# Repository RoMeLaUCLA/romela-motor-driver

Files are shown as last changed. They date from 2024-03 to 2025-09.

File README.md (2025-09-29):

# RoMeLa motor driver gen2
 Motor driver PCB and firmware designed for RoMeLa actuators. 
 
 Block diagram of the hardware:
 
 

 ## System Diagram

 
 
 # PCB reference

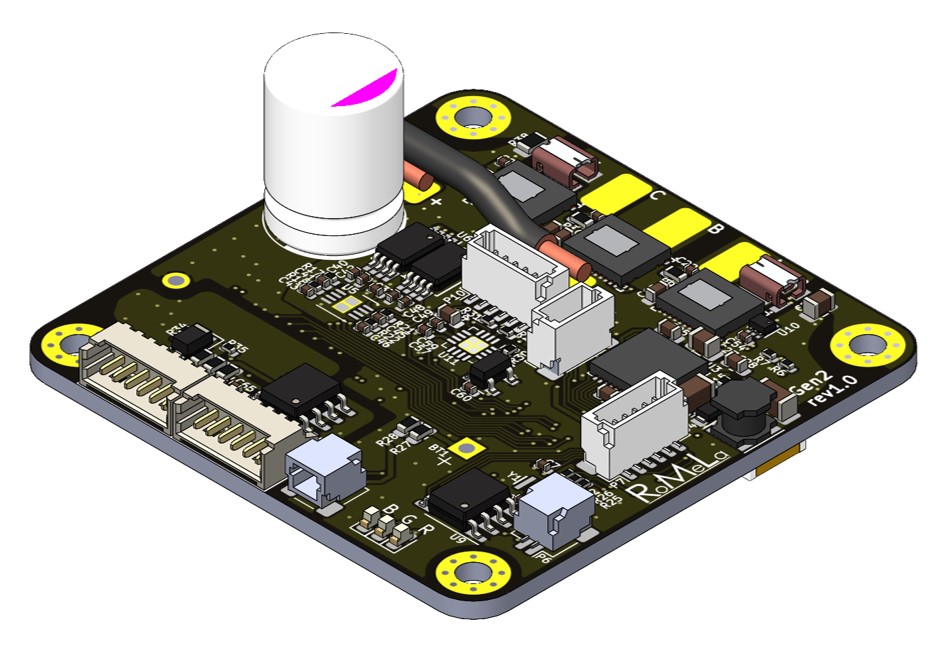
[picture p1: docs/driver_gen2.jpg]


[Link to gen2 schematics](/pcb/rev1/schematics_Motor_Gen2.pdf)

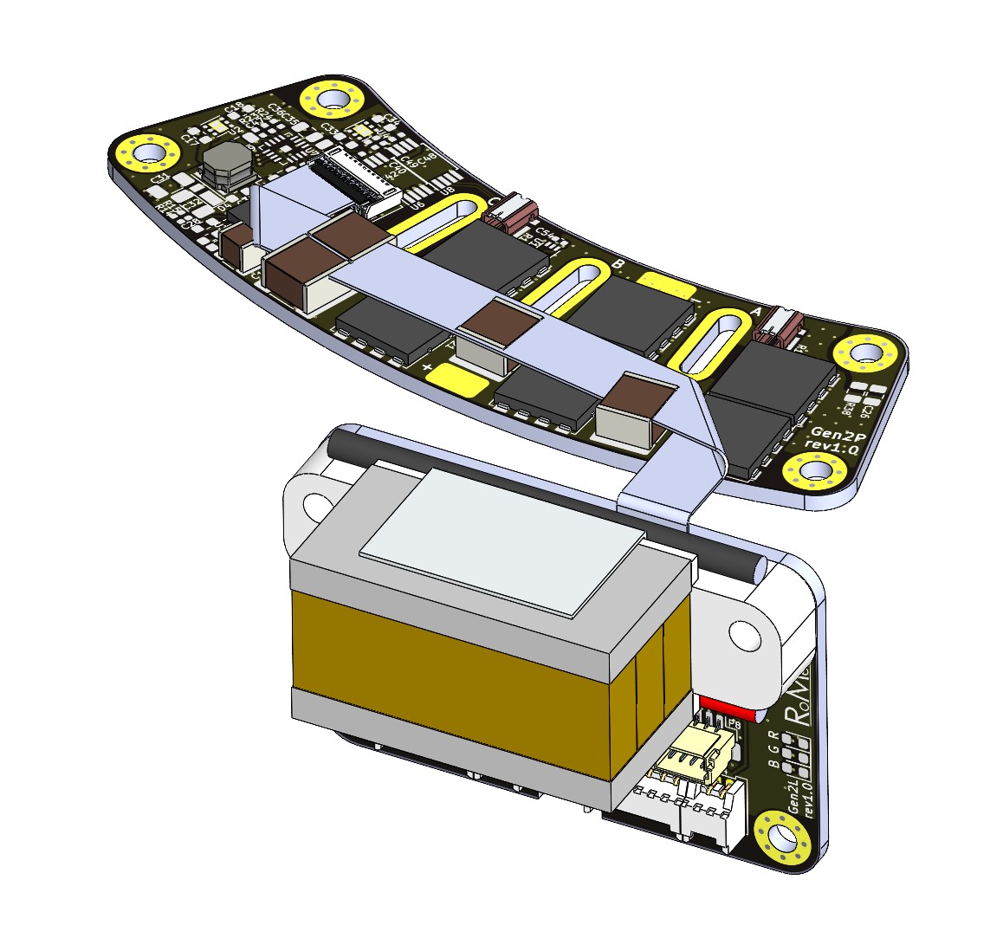
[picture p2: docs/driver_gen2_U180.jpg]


[Link to gen2L schematics](/pcb/split/gen2L/schematics_Motor_Gen2L.pdf)

[Link to gen2P schematics](/pcb/split/gen2P/schematics_Motor_Gen2P.pdf)

# Change Log
12/1/2022 Ver. 581
- First version using gcc(STM32CubeIDE)

04/13/2022 Ver. 48D
- Added 0.5ms de-glitch time for E-Stop input and 1sec minimum E-Stop time.

02/09/2022 Ver. 449
- Fixed MCU lock up with RS-485 over run present in Ver. 2BB.

09/27/2021 Ver. 33B
- Random ABS Posi error and Init error on power-up.

05/27/2021 Ver. 2BB
- Fixed cogging torque comp. issue.

03/31/2021 Ver. 27F
- Limit Id Max changed to Limit Acc Max
- Limit Iq Max changed to Limit I Max
- Added external Estop signal (wiring change) and command
- Acceleration limited S curve added to Mode 2 (position mode).
- Goal velocity and Iq feedforward term enabled for Mode 3. (Allow Id, Iq, Velocity, Position reference all at once)

09/29/2020 Ver. 130-137
- Added support for KB01_R18 and KB01_R24. (External AS5047 Encoder)

06/23/2020 Ver. D7
- Fixed joint limit issue.

05/20/2020 Ver. B4
- GEN2 Initial release.

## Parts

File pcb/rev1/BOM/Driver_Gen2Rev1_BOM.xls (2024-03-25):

Manufacturer | Manufacturer Part Number | Designator | Qty | Description | Case | SMD ,BGA,LLC(QFN),ORTH | Top/Bottom | points | Total points | polarity | Notes | Comments
Samsung Electro-Mechanics | CL05B104KO5NFNC | C1-C5, C7, C16, C37, C40, C48, C50, C54, C55, C57, C59, C60, C62, C63, C65 | 19 | 0.1µF ±10% 16V Ceramic Capacitor X7R 0402 | 0402 | SMD | Top and Bottom | 2 | 38 |  | Alternative parts accepted upon approval
 |  | C8 | 1 | D.N.P.
TDK Corporation | C5750X7S2A106K230KE | C9-C15 | 7 | 10µF ±10% 100V Ceramic Capacitor X7S 2220 | 2220 | SMD | Bottom | 2 | 14 |  | Alternative parts accepted upon approval
Samsung Electro-Mechanics | CL10B103KC8WPNC | C19-C21 | 3 | 10000pF ±10% 100V Ceramic Capacitor X7R 0603 | 0603 | SMD | Top | 2 | 6 |  | Alternative parts accepted upon approval
Murata Electronics | GCM155R72A472KA37D | C22-C24 | 3 | 4700pF ±10% 100V Ceramic Capacitor X7R 0402 | 0402 | SMD | Top | 2 | 6 |  | Alternative parts accepted upon approval
Samsung Electro-Mechanics | CL10B104KC8NNNC | C25 | 1 | 0.1µF ±10% 100V Ceramic Capacitor X7R 0603 | 0603 | SMD | Top | 2 | 2 |  | Alternative parts accepted upon approval
KEMET | C0805W472KDRACTU | C26 | 1 | 4700pF ±10% 1000V (1kV) Ceramic Capacitor X7R 0805 | 0805 | SMD | Top | 2 | 2 |  | Alternative parts accepted upon approval
Samsung Electro-Mechanics | CL21B105KOFNNNG | C27 | 1 | 1µF ±10% 16V Ceramic Capacitor X7R 0805 | 0805 | SMD | Top | 2 | 2 |  | Alternative parts accepted upon approval
TDK Corporation | C1608X7S2A473K080AB | C28 | 1 | 0.047µF ±10% 100V Ceramic Capacitor X7S 0603 | 0603 | SMD | Top | 2 | 2 |  | Alternative parts accepted upon approval
Samsung Electro-Mechanics | CL10B105KP8NFNC | C17, C18, C29, C33, C34, C58 | 6 | 1µF ±10% 10V Ceramic Capacitor X7R 0603 | 0603 | SMD | Top and Bottom | 2 | 12 |  | Alternative parts accepted upon approval
Samsung Electro-Mechanics | CL10B334KO8NFNC | C30 | 1 | 0.33µF ±10% 16V Ceramic Capacitor X7R 0603 | 0603 | SMD | Bottom | 2 | 2 |  | Alternative parts accepted upon approval
Samsung Electro-Mechanics | CL31B226KPHNNNE | C31, C61, C64 | 3 | 22µF ±10% 10V Ceramic Capacitor X7R 1206 | 1206 | SMD | Top and Bottom | 2 | 6 |  | Alternative parts accepted upon approval
TDK Corporation | CGA5L3X7S2A225K160AB | C32 | 1 | 2.2µF ±10% 100V Ceramic Capacitor X7S 1206 | 1206 | SMD | Top | 2 | 2 |  | Alternative parts accepted upon approval
Samsung Electro-Mechanics | CL21B106KPQNFNE | C6, C35, C36, C38, C39, C56 | 6 | 10µF ±10% 10V Ceramic Capacitor X7R 0805 | 0805 | SMD | Bottom | 2 | 12 |  | Alternative parts accepted upon approval
Samsung Electro-Mechanics | CL05B103KB5NNNC | C42, C49, C51-C53 | 5 | 10000pF ±10% 50V Ceramic Capacitor X7R 0402 | 0402 | SMD | Top and Bottom | 2 | 10 |  | Alternative parts accepted upon approval
Murata Electronics | GRM1555C1H102JA01J | C43, C46 | 2 | 1000pF ±5% 50V Ceramic Capacitor C0G, NP0 0402 | 0402 | SMD | Top | 2 | 4 |  | Alternative parts accepted upon approval
KEMET | C0402C152J5GAC7867 | C41, C44, C45, C47 | 4 | 1500pF ±5% 50V Ceramic Capacitor C0G, NP0 0402 | 0402 | SMD | Top and Bottom | 2 | 8 |  | Alternative parts accepted upon approval
Rohm Semiconductor | SML-D12U1WT86 | D1 | 1 | Red 620nm LED Indication - Discrete 2.2V 0603 | 0603 | SMD | Top | 2 | 2 | Yes | Alternative parts accepted upon approval
Rohm Semiconductor | SML-D13M8WT86 | D2 | 1 | Green 572nm LED Indication - Discrete 2.2V 0603 | 0603 | SMD | Top | 2 | 2 | Yes | Alternative parts accepted upon approval
Rohm Semiconductor | SMLD12BN1WT86 | D3 | 1 | Blue 470nm LED Indication - Discrete 2.9V 0603 | 0603 | SMD | Top | 2 | 2 | Yes | Alternative parts accepted upon approval
Vishay Semiconductor Diodes Division | V1PM10-M3/H | D4 | 1 | Diode Schottky 100V 1A | DO-219AD | SMD | Top | 2 | 2 | Yes
STMicroelectronics | ESDCAN02-2BWY | D5 | 1 | 44V Clamp 3A (8/20µs) Ipp Tvs Diode Surface Mount SOT-323-3 | SOT-323 | SMD | Bottom | 3 | 3
Littelfuse Inc. | SMF3.3 | D6 | 1 | 6.8V Clamp 30A Ipp Tvs Diode | SOD-123F | SMD | Top | 2 | 2 | Yes
Bel Fuse Inc. | 0ZCM0002FF2G | F1 | 1 | PTC Resettable Fuse 60V 20mA 0603 | 0603 | SMD | Top | 2 | 2
Murata Electronics | BLM15PX601SN1D | FB1, FB2 | 2 | 600 Ohms Ferrite Bead 0402 230mOhm | 0402 | SMD | Bottom | 2 | 4 |  | Alternative parts accepted upon approval
 |  | J1, J2 | 2 | D.N.P.
Laird-Signal Integrity Products | TYS4030220M-10 | L1 | 1 | 22µH Shielded Wirewound Inductor 1A | 4mmx4mm | SMD | Top | 2 | 2
JST Sales America Inc. | SM02B-SRSS-TB(LF)(SN) | P5, P6 | 2 | Connector Header Surface Mount, Right Angle 2 position 1.00mm | Header 2pin | SMD | Top | 4 | 8
JST Sales America Inc. | BM06B-SRSS-TBT(LF)(SN) | P7, P10 | 2 | Connector Header Surface Mount 6 position 1.00mm | header 6pin | SMD | Top | 8 | 16
JST Sales America Inc. | BM04B-SRSS-TBT(LF)(SN) | P8 | 1 | Connector Header Surface Mount 4 position 1.00mm | Header 4pin | SMD | Top | 6 | 6
Molex | 0545500871 | P9 | 1 | 8 Position FFC Top 0.50mm Surface Mount, Right Angle | FFC header | SMD | Bottom | 10 | 10
Texas Instruments | CSD88599Q5DC | Q1-Q3 | 3 | Mosfet Array 2 N-Channel (Half Bridge) 60V 12W Surface Mount 22-VSON-CLIP (5x6) | 22-VSON-CLIP (5x6) | VSON | Top | 11 | 33 | Yes
Rohm Semiconductor | ESR03EZPJ121 | R1, R3, R4, R27, R28 | 5 | 120 Ohms ±5% 0.25W 0603 Pulse Withstanding | 0603 | SMD | Top and Bottom | 2 | 10
Bourns Inc. | CR0402-FX-1302GLF | R2, R15, R18, R22, R30, R31 | 6 | 13 kOhms ±1% 0.063W, 1/16W Chip Resistor 0402 | 0402 | SMD | Top | 2 | 12 |  | Alternative parts accepted upon approval
Bourns Inc. | CR0603-JW-470ELF | R5 | 1 | 47 Ohms ±5% 0.1W, 1/10W Chip Resistor 0603 | 0603 | SMD | Bottom | 2 | 2 |  | Alternative parts accepted upon approval
Bourns Inc. | CR0402-FX-7502GLF | R6, R14, R34 | 3 | 75 kOhms ±1% 0.063W, 1/16W Chip Resistor 0402 | 0402 | SMD | Top | 2 | 6 |  | Alternative parts accepted upon approval
Bourns Inc. | CR0402-FX-3901GLF | R7, R25, R26, R35 | 4 | 3.9 kOhms ±1% 0.063W, 1/16W Chip Resistor 0402 | 0402 | SMD | Top | 2 | 8 |  | Alternative parts accepted upon approval
Bourns Inc. | CR0402-J/-000GLF | R8, R16, R29 | 3 | 0 Ohms Jumper 0402 | 0402 | SMD | Top and Bottom | 2 | 6 |  | Alternative parts accepted upon approval
Bourns Inc. | CR0603AF/-2R20EAS | R9-R11 | 3 | 2.2 Ohms ±1% 0.1W, 1/10W Chip Resistor 0603 | 0603 | SMD | Top | 2 | 6 |  | Alternative parts accepted upon approval
Vishay Dale | WSK12161L000FEA | R12, R13 | 2 | 1 mOhms ±1% 3W Chip Resistor Wide 1612 (3831 Metric) | Wide 1612 (3831 Metric) | SMD | Top | 4 | 8
Bourns Inc. | CR0402-FX-7501GLF | R17, R21 | 2 | 7.5 kOhms ±1% 0.063W, 1/16W Chip Resistor 0402 | 0402 | SMD | Top | 2 | 4 |  | Alternative parts accepted upon approval
Bourns Inc. | CR0402-FX-10R0GLF | R19, R20, R23, R24 | 4 | 10 Ohms ±1% 0.063W, 1/16W Chip Resistor 0402 | 0402 | SMD | Bottom | 2 | 8 |  | Alternative parts accepted upon approval
Rohm Semiconductor | ESR03EZPF10R0 | R32, R33 | 2 | 10 Ohms ±1% 0.25W 0603 Pulse Withstanding | 0603 | SMD | Top | 2 | 4
Rohm Semiconductor | ESR10EZPJ105 | R38 | 1 | 1 MOhms ±5% 0.4W, 2/5W Chip Resistor 0805 | 0805 | SMD | Top | 2 | 2
STMicroelectronics | STM32F446RET6 | U1 | 1 | ARM® Cortex®-M4 STM32F4 Microcontroller IC 32-Bit 180MHz 512KB (512K x 8) FLASH 64-LQFP (10x10) | LQFP-64 10x10mm P0.5mm | SMD | Bottom | 64 | 64 | Yes
Texas Instruments | TLV76733DRVR | U2 | 1 | Linear Voltage Regulator IC 3.3V 1A 6-WSON (2x2) | WSON-6 | WSON | Bottom | 7 | 7 | Yes
Texas Instruments | DRV8320RSRHAR | U3 | 1 | Multiphase Motor Driver Power MOSFET SPI 40-VQFN (6x6) | PVQFN-40 | QFN | Top | 41 | 41 | Yes
Texas Instruments | LP5912-5.0DRVR | U4 | 1 | Linear Voltage Regulator IC 5V 500mA 6-WSON (2x2) | WSON-6 | WSON | Bottom | 7 | 7 | Yes
Texas Instruments | OPA2320AIDRGR | U5 | 1 | General Purpose Amplifier 2 Circuit Rail-to-Rail 8-SON (3x3) | S-PWSON-N8 | WSON | Top | 9 | 9 | Yes
Texas Instruments | ADS8353IRTER | U7 | 1 | 16 Bit Analog to Digital Converter 2 Input 2 SAR 16-WQFN (3x3) | WQFN-16 | QFN | Bottom | 17 | 17 | Yes
Texas Instruments | INA240A1PWR | U6, U8 | 2 | Current Sense Amplifier 1 Circuit 8-TSSOP | TSSOP-8 | SMD | Top | 8 | 16 | Yes
Maxim Integrated | MAX31855KASA+T | U9 | 1 | IC CONV THERMOCOUPLE-DGTL 8SOIC | SOIC-8 | SMD | Top | 8 | 8 | Yes
Texas Instruments | TMP112NAIDRLR | U10 | 1 | Temperature Sensor Digital, Local -40°C ~ 125°C 12 b SOT-563 | SOT-563 | SMD | Top | 6 | 6 | Yes
iC-Haus | iC-PV | U11 | 1 | - | QFN-16 | QFN | Top | 17 | 17 | Yes | Provided by customer
iC-Haus | iC-MHM | U12 | 1 | - | QFN-28 | QFN | Bottom | 29 | 29 | Yes | Provided by customer
Microchip Technology | 24LC16BT-E/OT | U13 | 1 | EEPROM Memory IC 16Kb (2K x 8) I²C 400kHz 900ns SOT-23-5 | SOT-23-5 | SMD | Top | 5 | 5
Texas Instruments | ISOW7842FDWE | U14 | 1 | General Purpose Digital Isolator 5000Vrms 4 Channel 100Mbps 100kV/µs CMTI 16-SOIC | SOIC-16W | SMD | Bottom | 16 | 16 | Yes
Maxim Integrated | MAX14775EASA+ | U15 | 1 | 1/1 Transceiver Half RS422, RS485 8-SOIC | 8-SOIC | SMD | Top | 8 | 8 | Yes
Murata Electronics | CSTNE8M00GH5C000R0 | Y1 | 1 | 8MHz Ceramic Resonator Built in Capacitor 33pF ±0.13% 40 Ohms -40°C ~ 125°C Surface Mount | 3.2mmx1.3mm | SMD | Top | 3 | 3

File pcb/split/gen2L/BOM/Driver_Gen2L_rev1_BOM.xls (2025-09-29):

Manufacturer | Manufacturer Part Number | Designator | Qty | Description | Case | SMD ,BGA,LLC(QFN),ORTH | Top/Bottom | points | Total points | polarity | Notes | Comments
Samsung Electro-Mechanics | CL21B106KPQNFNE | C6 | 1 | 10µF ±10% 10V Ceramic Capacitor X7R 0805 | 0805 | SMD | Bottom | 2 | 2 |  | Alternative parts accepted upon approval
Samsung Electro-Mechanics | CL05B104KA5NNNC | C1-C5, C7, C16, C50, C62, C63, C65 | 11 | 0.1 µF ±10% 25V Ceramic Capacitor X7R 0402 (1005 Metric) | 0402 | SMD | Top/Bottom | 2 | 22 |  | Alternative parts accepted upon approval
Samsung Electro-Mechanics | CL05B103KB5NNNC | C51-C53 | 3 | 10000pF ±10% 50V Ceramic Capacitor X7R 0402 | 0402 | SMD | Bottom | 2 | 6 |  | Alternative parts accepted upon approval
Samsung Electro-Mechanics | CL31B226KPHNNNE | C61, C64 | 2 | 22µF ±10% 10V Ceramic Capacitor X7R 1206 | 1206 | SMD | Bottom | 2 | 4 |  | Alternative parts accepted upon approval
Rohm Semiconductor | SML-D12U1WT86 | D1 | 1 | Red 620nm LED Indication - Discrete 2.2V 0603 | 0603 | SMD | Top | 2 | 2 | Yes | Alternative parts accepted upon approval
Rohm Semiconductor | SML-D13M8WT86 | D2 | 1 | Green 572nm LED Indication - Discrete 2.2V 0603 | 0603 | SMD | Top | 2 | 2 | Yes | Alternative parts accepted upon approval
Rohm Semiconductor | SMLD12BN1WT86 | D3 | 1 | Blue 470nm LED Indication - Discrete 2.9V 0603 | 0603 | SMD | Top | 2 | 2 | Yes | Alternative parts accepted upon approval
STMicroelectronics | ESDCAN02-2BWY | D5 | 1 | 44V Clamp 3A (8/20µs) Ipp Tvs Diode Surface Mount SOT-323-3 | SOT-323 | SMD | Top | 3 | 3
Littelfuse Inc. | SMF3.3 | D6 | 1 | 6.8V Clamp 30A Ipp Tvs Diode | SOD-123F | SMD | Bottom | 2 | 2 | Yes | Alternative: PTVS3V3S1UTR,115
Bel Fuse Inc. | 0ZCM0002FF2G | F1 | 1 | PTC Resettable Fuse 60V 20mA 0603 | 0603 | SMD | Bottom | 2 | 2
Murata Electronics | BLM15PX601SN1D | FB1, FB2 | 2 | 600 Ohms Ferrite Bead 0402 230mOhm | 0402 | SMD | Bottom | 2 | 4 |  | Alternative parts accepted upon approval
Molex | 5019122190 | J1 | 1 | 21 Position FPC Connector Contacts, Bottom 0.012" (0.30mm) Surface Mount, Right Angle | FPC 21POS | SMD | Top | 23 | 23
Molex | 5034800800 | J2, P9 | 2 | 8 Position FFC, FPC Connector Contacts, Top and Bottom 0.020" (0.50mm) Surface Mount, Right Angle | FPC 8POS | SMD | Top | 10 | 20
Molex | 0530480650 | P1, P2 | 2 | Connector Header Through Hole, Right Angle 6 position 0.049" (1.25mm) | Header R/A 6POS | TH | Top | 6 | 12
Molex | 0530480250 | P4, P5 | 2 | Connector Header Through Hole, Right Angle 2 position 0.049" (1.25mm) | Header R/A 2POS | TH | Top | 2 | 4
JST Sales America Inc. | SM02B-SRSS-TB(LF)(SN) | P6 | 1 | Connector Header Surface Mount, Right Angle 2 position 1.00mm | Header 2pin | SMD | Top | 4 | 4
JST Sales America Inc. | BM06B-SRSS-TB(LF)(SN) | P7, P10 | 2 | Connector Header Surface Mount 6 position 1.00mm | header 6pin | SMD | Top | 8 | 16
JST Sales America Inc. | BM04B-SRSS-TB(LF)(SN) | P8 | 1 | Connector Header Surface Mount 4 position 1.00mm | Header 4pin | SMD | Top | 6 | 6
Rohm Semiconductor | ESR03EZPJ121 | R1, R3, R4 | 3 | 120 Ohms ±5% 0.25W 0603 Pulse Withstanding | 0603 | SMD | Top/Bottom | 2 | 6 |  | Alternative parts accepted upon approval
Bourns Inc. | CR0402-FX-1302GLF | R2 | 1 | 13 kOhms ±1% 0.063W, 1/16W Chip Resistor 0402 | 0402 | SMD | Bottom | 2 | 2 |  | Alternative parts accepted upon approval
Bourns Inc. | CR0603-JW-470ELF | R5 | 1 | 47 Ohms ±5% 0.1W, 1/10W Chip Resistor 0603 | 0603 | SMD | Bottom | 2 | 2 |  | Alternative parts accepted upon approval
Bourns Inc. | CR0402-FX-3901GLF | R25, R26, R35 | 3 | 3.9 kOhms ±1% 0.063W, 1/16W Chip Resistor 0402 | 0402 | SMD | Top/Bottom | 2 | 6 |  | Alternative parts accepted upon approval
Rohm Semiconductor | ESR03EZPF10R0 | R32, R33 | 2 | 10 Ohms ±1% 0.25W 0603 Pulse Withstanding | 0603 | SMD | Top | 2 | 4 |  | Alternative parts accepted upon approval
Bourns Inc. | CR0402-FX-7502GLF | R34 | 1 | 75 kOhms ±1% 0.063W, 1/16W Chip Resistor 0402 | 0402 | SMD | Top | 2 | 2 |  | Alternative parts accepted upon approval
STMicroelectronics | STM32F446RET6 | U1 | 1 | ARM® Cortex®-M4 STM32F4 Microcontroller IC 32-Bit 180MHz 512KB (512K x 8) FLASH 64-LQFP (10x10) | LQFP-64 10x10mm P0.5mm | SMD | Bottom | 64 | 64 | Yes | Provided by customer
Maxim Integrated | MAX31855KASA+T | U9 | 1 | IC CONV THERMOCOUPLE-DGTL 8SOIC | SOIC-8 | SMD | Bottom | 8 | 8 | Yes | Provided by customer
Texas Instruments | ISOW7842FDWE | U14 | 1 | General Purpose Digital Isolator 5000Vrms 4 Channel 100Mbps 100kV/µs CMTI 16-SOIC | SOIC-16W | SMD | Bottom | 16 | 16 | Yes | Provided by customer
Maxim Integrated | MAX14775EASA+ | U15 | 1 | 1/1 Transceiver Half RS422, RS485 8-SOIC | 8-SOIC | SMD | Top | 8 | 8 | Yes | Provided by customer
Murata Electronics | CSTNE8M00GH5C000R0 | Y1 | 1 | 8MHz Ceramic Resonator Built in Capacitor 33pF ±0.13% 40 Ohms -40°C ~ 125°C Surface Mount | 3.2mmx1.3mm | SMD | Top | 3 | 3

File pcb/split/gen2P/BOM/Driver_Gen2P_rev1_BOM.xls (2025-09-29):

Manufacturer | Manufacturer Part Number | Designator | Qty | Description | Case | SMD ,BGA,LLC(QFN),ORTH | Top/Bottom | points | Total points | polarity | Notes | Comments
TDK Corporation | C5750X7S2A226M280KB | C9-C12 | 4 | 22 µF ±20% 100V Ceramic Capacitor X7S 2220 (5750 Metric) | 2220 | SMD | Top | 2 | 8 |  | Provided by customer
Murata Electronics | GRM32EC72A106KE05L | C15 | 1 | 10 µF ±10% 100V Ceramic Capacitor X7S 1210 (3225 Metric) | 1210 | SMD | Top | 2 | 2 |  | Alternative parts accepted upon approval
Samsung Electro-Mechanics | CL10B103KC8WPNC | C19-C21 | 3 | 10000pF ±10% 100V Ceramic Capacitor X7R 0603 | 0603 | SMD | Top | 2 | 6 |  | Alternative parts accepted upon approval
Samsung Electro-Mechanics | CL10B104KC8NNNC | C25 | 1 | 0.1µF ±10% 100V Ceramic Capacitor X7R 0603 | 0603 | SMD | Top | 2 | 2 |  | Alternative parts accepted upon approval
KEMET | C0805W472KDRACTU | C26 | 1 | 4700pF ±10% 1000V (1kV) Ceramic Capacitor X7R 0805 | 0805 | SMD | Top | 2 | 2 |  | Alternative parts accepted upon approval
Murata Electronics | GRM188Z71C225ME43J | C27 | 1 | 2.2 µF ±20% 16V Ceramic Capacitor X7R 0603 (1608 Metric) | 0603 | SMD | Top | 2 | 2 |  | Alternative parts accepted upon approval
Würth Elektronik | 885012206118 | C28 | 1 | 0.047 µF ±10% 100V Ceramic Capacitor X7R 0603 (1608 Metric) | 0603 | SMD | Top | 2 | 2 |  | Alternative parts accepted upon approval
Samsung Electro-Mechanics | CL10B105KP8NFNC | C17, C18, C29, C33, C34 | 5 | 1µF ±10% 10V Ceramic Capacitor X7R 0603 | 0603 | SMD | Top | 2 | 10 |  | Alternative parts accepted upon approval
Samsung Electro-Mechanics | CL10B334KO8NFNC | C30 | 1 | 0.33µF ±10% 16V Ceramic Capacitor X7R 0603 | 0603 | SMD | Top | 2 | 2 |  | Alternative parts accepted upon approval
Samsung Electro-Mechanics | CL31B226KPHNNNE | C31 | 1 | 22µF ±10% 10V Ceramic Capacitor X7R 1206 | 1206 | SMD | Top | 2 | 2 |  | Alternative parts accepted upon approval
Samsung Electro-Mechanics | CL31B225KCHSNNE | C32 | 1 | 2.2 µF ±10% 100V Ceramic Capacitor X7R 1206 (3216 Metric) | 1206 | SMD | Top | 2 | 2 |  | Alternative parts accepted upon approval
Samsung Electro-Mechanics | CL21B106KPQNFNE | C35, C36, C38, C39 | 4 | 10µF ±10% 10V Ceramic Capacitor X7R 0805 | 0805 | SMD | Top | 2 | 8 |  | Alternative parts accepted upon approval
Samsung Electro-Mechanics | CL05B104KA5NNNC | C40, C48, C54 | 3 | 0.1 µF ±10% 25V Ceramic Capacitor X7R 0402 (1005 Metric) | 0402 | SMD | Top | 2 | 6 |  | Alternative parts accepted upon approval
Samsung Electro-Mechanics | CL05B103KB5NNNC | C42, C49 | 2 | 10000pF ±10% 50V Ceramic Capacitor X7R 0402 | 0402 | SMD | Top | 2 | 4 |  | Alternative parts accepted upon approval
Murata Electronics | GRM1555C1H102JA01D | C44, C47 | 2 | 1000 pF ±5% 50V Ceramic Capacitor C0G, NP0 0402 (1005 Metric) | 0402 | SMD | Top | 2 | 4 |  | Alternative parts accepted upon approval
Vishay General Semiconductor - Diodes Division | V1PM10HM3/H | D4 | 1 | Diode Schottky 100 V 1A Surface Mount MicroSMP (DO-219AD) | DO-219AD | SMD | Top | 2 | 2 | Yes
Molex | 5019122190 | J1 | 1 | 21 Position FPC Connector Contacts, Bottom 0.012" (0.30mm) Surface Mount, Right Angle | FPC 21POS | SMD | Top | 23 | 23
Taiyo Yuden | MDWK4040T220MM | L1 | 1 | 22 µH Shielded Drum Core, Wirewound Inductor 1.2 A 460mOhm Max Nonstandard | 4mmx4mm | SMD | Top | 2 | 2
onsemi | NTMTS001N06CTXG | Q1-Q6 | 6 | N-Channel 60 V 53.7A (Ta), 376A (Tc) 5W (Ta), 244W (Tc) Surface Mount 8-DFNW (8.3x8.4) | 8-PowerTDFN | TDFN | Top | 5 | 30
Bourns Inc. | CR0402-FX-7502GLF | R6, R14 | 1 | 75 kOhms ±1% 0.063W, 1/16W Chip Resistor 0402 | 0402 | SMD | Top | 2 | 2 |  | Alternative parts accepted upon approval
Bourns Inc. | CR0402-FX-3901GLF | R7 | 1 | 3.9 kOhms ±1% 0.063W, 1/16W Chip Resistor 0402 | 0402 | SMD | Top | 2 | 2 |  | Alternative parts accepted upon approval
Stackpole Electronics Inc | HCSK1216FTL500 | R12, R13 | 2 | 0.5 mOhms ±1% 5W Chip Resistor Nonstandard Current Sense, Moisture Resistant Metal Element | 1216 | SMD | Top | 2 | 4 |  | Alternative part: WSK1216L5000FEA
Bourns Inc. | CR0402-FX-1302GLF | R15 | 1 | 13 kOhms ±1% 0.063W, 1/16W Chip Resistor 0402 | 0402 | SMD | Top | 2 | 2 |  | Alternative parts accepted upon approval
Bourns Inc. | CR0402-FX-33R0GLF | R19, R20, R23, R24 | 4 | 33 Ohms ±1% 0.063W, 1/16W Chip Resistor 0402 (1005 Metric) Thick Film | 0402 | SMD | Top | 2 | 8 |  | Alternative parts accepted upon approval
Rohm Semiconductor | ESR10EZPJ105 | R38 | 1 | 1 MOhms ±5% 0.4W, 2/5W Chip Resistor 0805 | 0805 | SMD | Top | 2 | 2 |  | Alternative parts accepted upon approval
Texas Instruments | TLV76733DRVR | U2 | 1 | Linear Voltage Regulator IC 3.3V 1A 6-WSON (2x2) | WSON-6 | WSON | Top | 7 | 7 | Yes
Texas Instruments | DRV8320RSRHAR | U3 | 1 | Multiphase Motor Driver Power MOSFET SPI 40-VQFN (6x6) | PVQFN-40 | QFN | Top | 41 | 41 | Yes | Alternative part: DRV8320RSRHAT
Texas Instruments | LP5912-5.0DRVR | U4 | 1 | Linear Voltage Regulator IC 5V 500mA 6-WSON (2x2) | WSON-6 | WSON | Top | 7 | 7 | Yes
Texas Instruments | ADS8353IRTER | U7 | 1 | 16 Bit Analog to Digital Converter 2 Input 2 SAR 16-WQFN (3x3) | WQFN-16 | QFN | Top | 17 | 17 | Yes | Provided by customer
Texas Instruments | INA240A1PWR | U6, U8 | 2 | Current Sense Amplifier 1 Circuit 8-TSSOP | TSSOP-8 | SMD | Top | 8 | 16 | Yes | Provided by customer
Texas Instruments | TMP112NAIDRLR | U10 | 1 | Temperature Sensor Digital, Local -40°C ~ 125°C 12 b SOT-563 | SOT-563 | SMD | Top | 6 | 6 | Yes

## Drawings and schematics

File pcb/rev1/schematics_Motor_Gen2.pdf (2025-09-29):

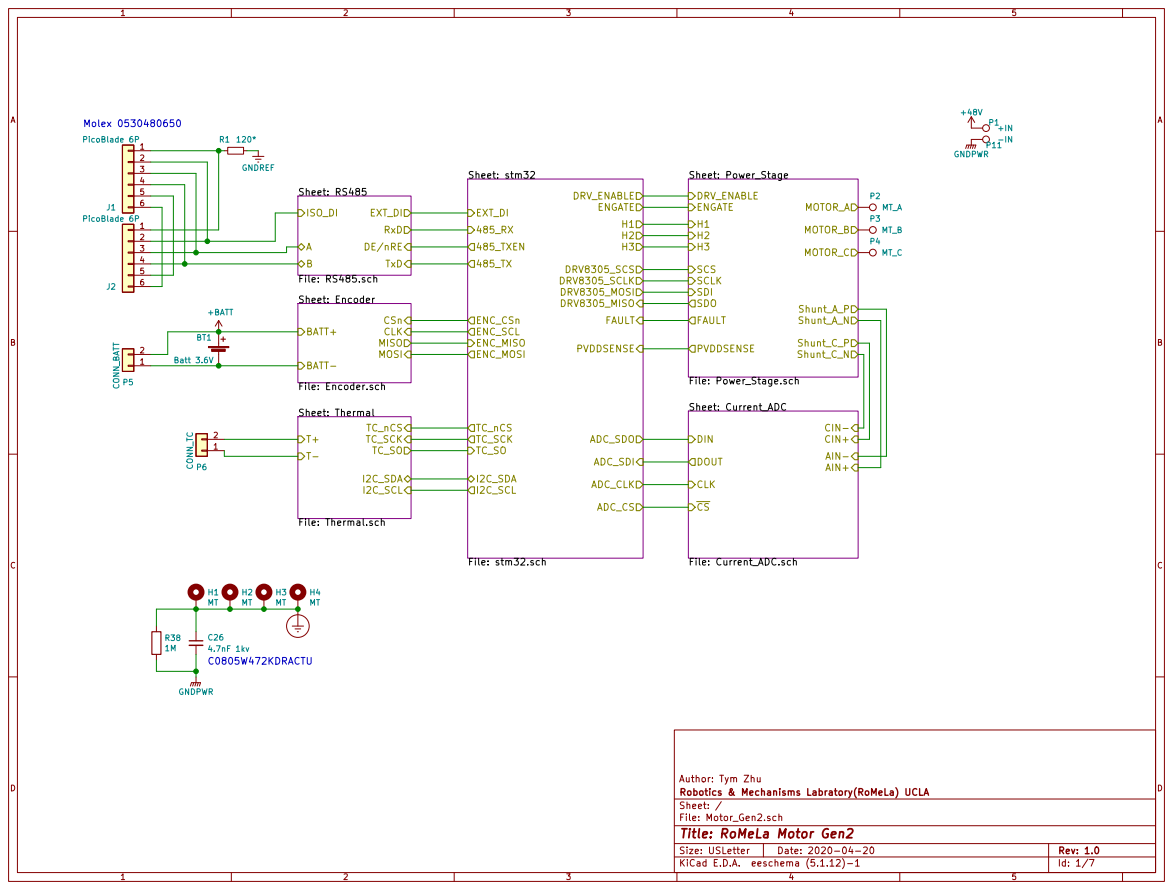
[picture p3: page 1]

FAULT SCLK SDO | MOTOR_A MOTOR_B MOTOR_C Shunt_A_P Shunt_C_P

3 4

MISO

Author: Tym Zhu
File: Motor_Gen2.sch Sheet: / Robotics & Mechanisms Labratory(RoMeLa) UCLA

Id: 1/7 Title: RoMeLa Motor Gen2

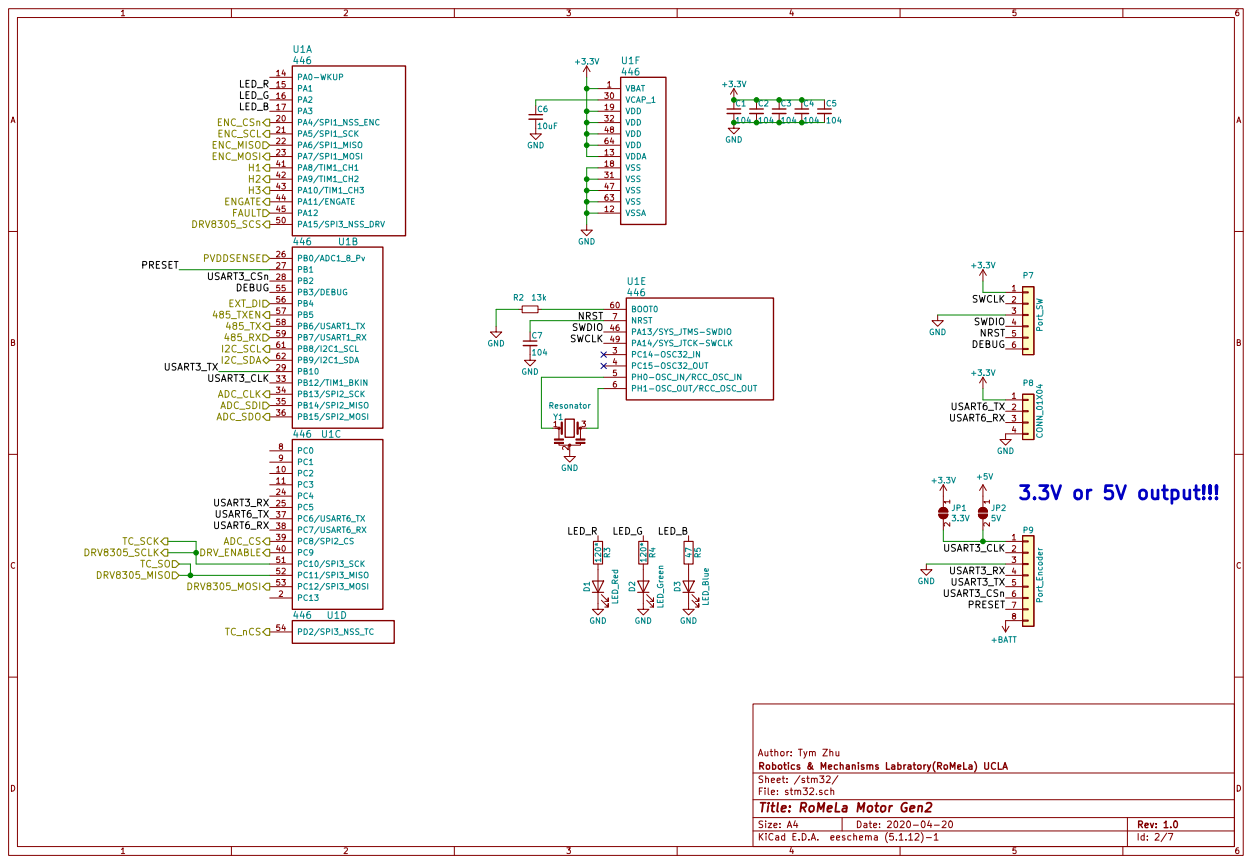
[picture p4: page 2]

Author: Tym Zhu
File: stm32.sch Sheet: /stm32/ Robotics & Mechanisms Labratory(RoMeLa) UCLA

Id: 2/7 Title: RoMeLa Motor Gen2

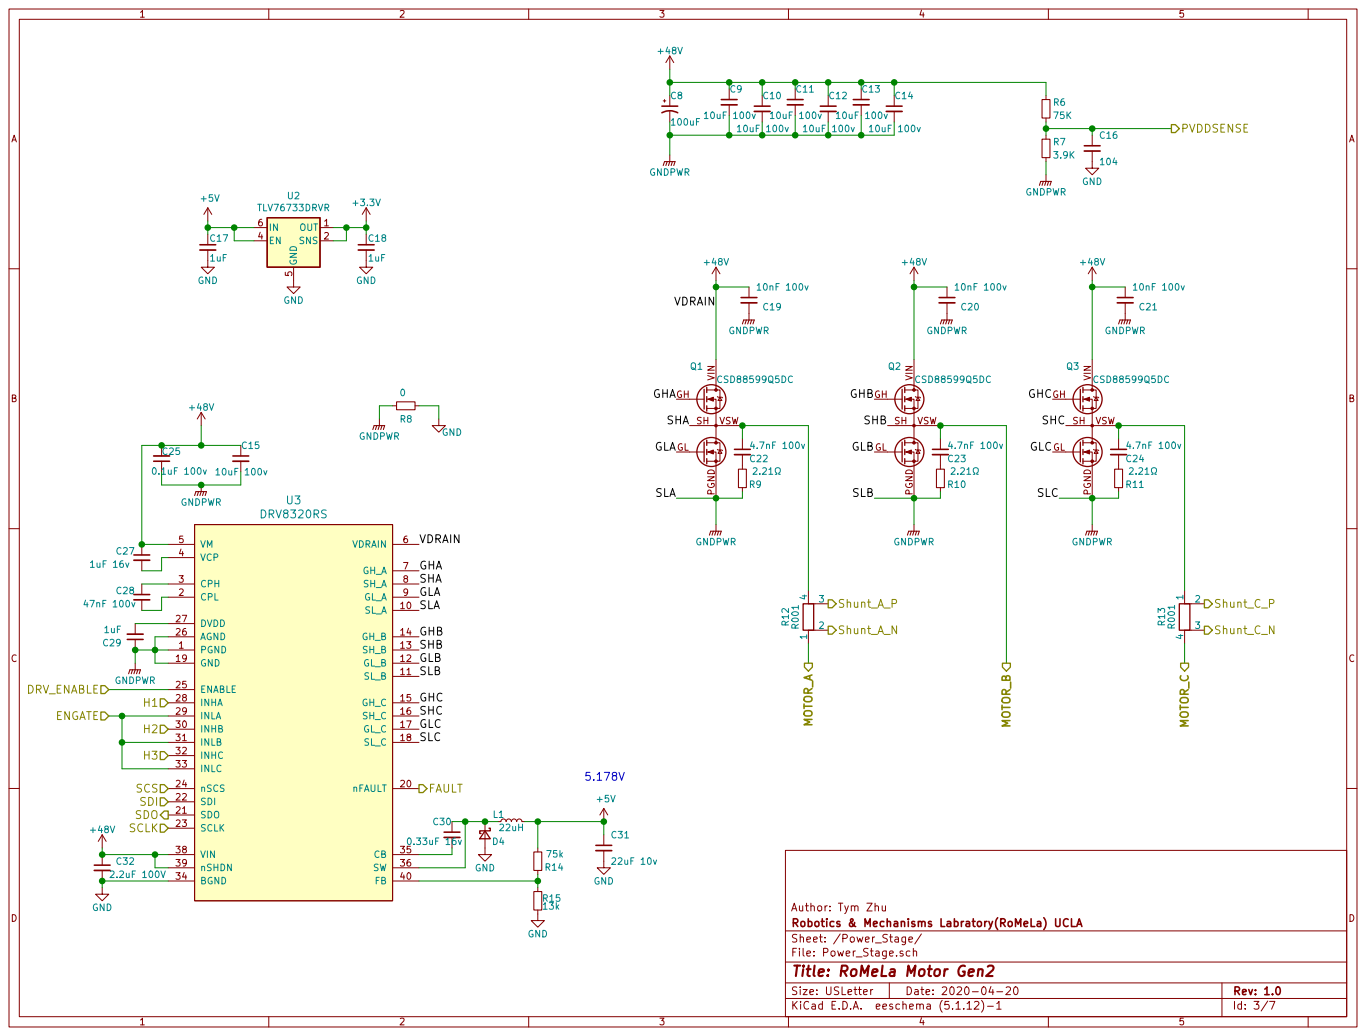
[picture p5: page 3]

Robotics & Mechanisms Labratory(RoMeLa) UCLA
Sheet: /Power_Stage/
File: Power_Stage.sch
Id: 3/7 Title: RoMeLa Motor Gen2

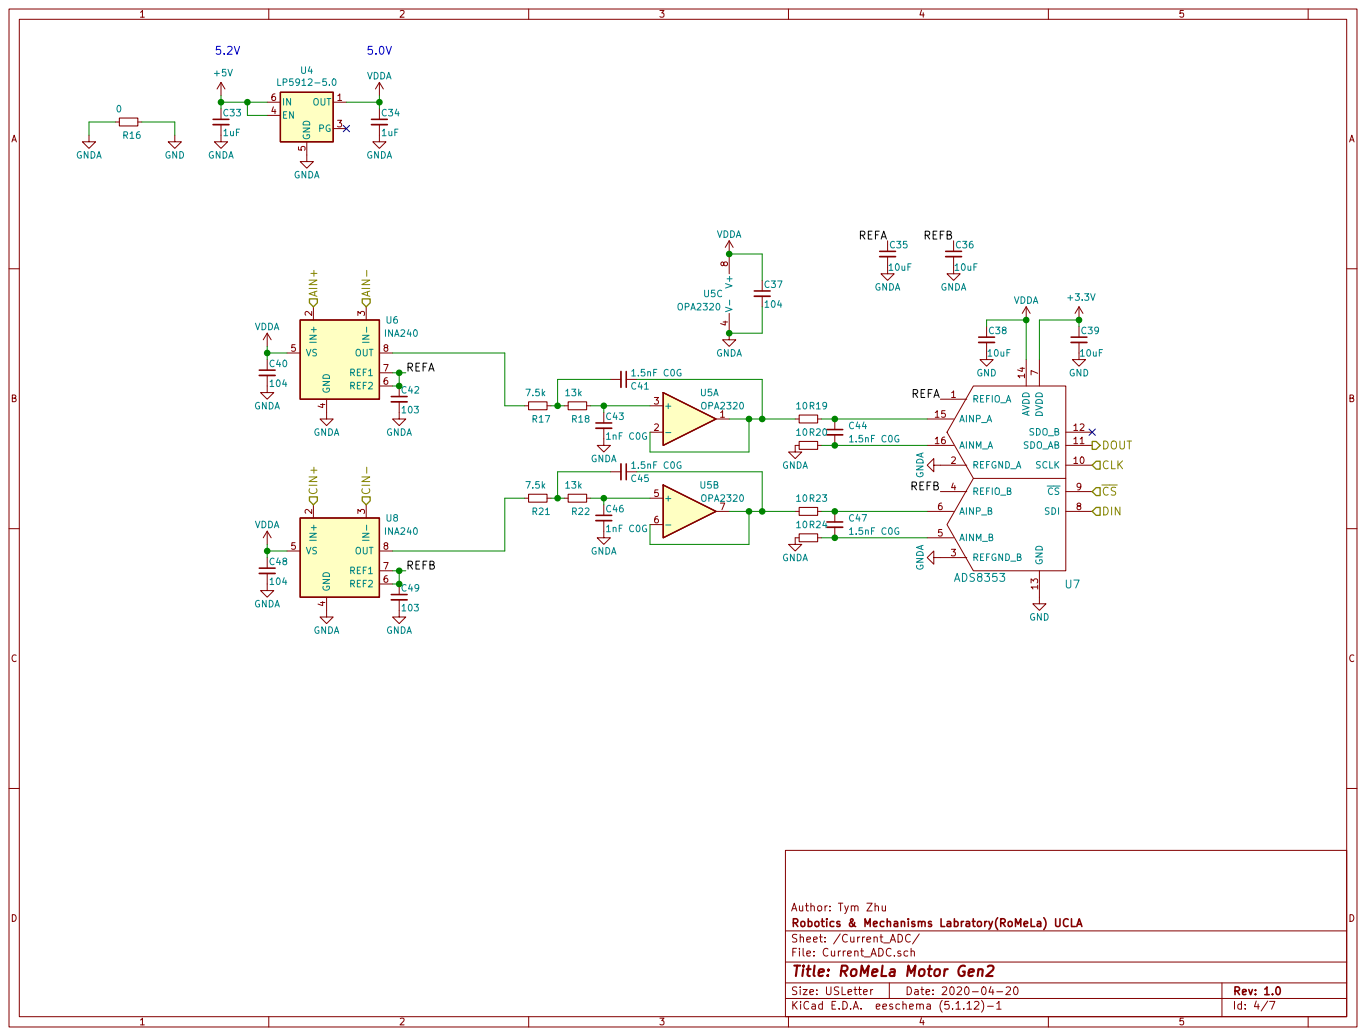
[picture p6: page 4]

Author: Tym Zhu
Robotics & Mechanisms Labratory(RoMeLa) UCLA
Sheet: /Current_ADC/
File: Current_ADC.sch
Id: 4/7 Title: RoMeLa Motor Gen2

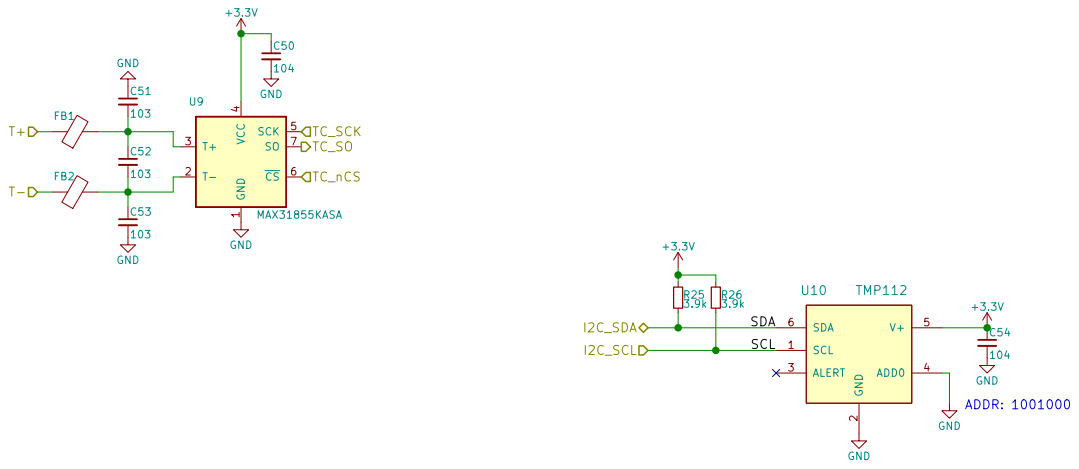
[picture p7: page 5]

Author: Tym Zhu GND

File: Thermal.sch Sheet: /Thermal/ Robotics & Mechanisms Labratory(RoMeLa) UCLA

Id: 5/7 Title: RoMeLa Motor Gen2

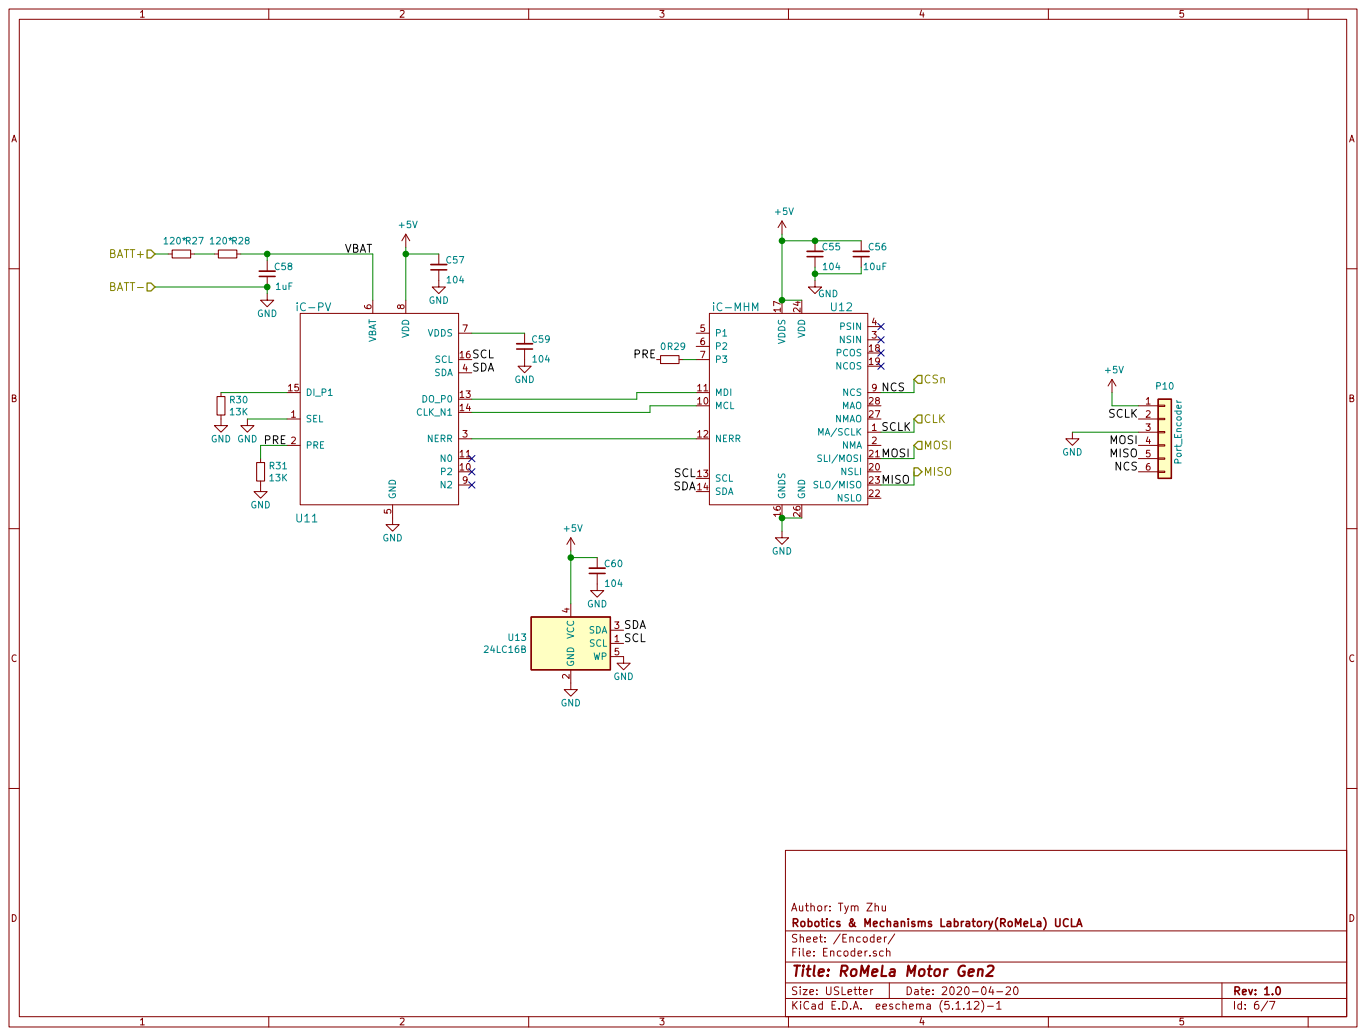
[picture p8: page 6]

File: Encoder.sch Sheet: /Encoder/ Robotics & Mechanisms Labratory(RoMeLa) UCLA

Id: 6/7 Title: RoMeLa Motor Gen2

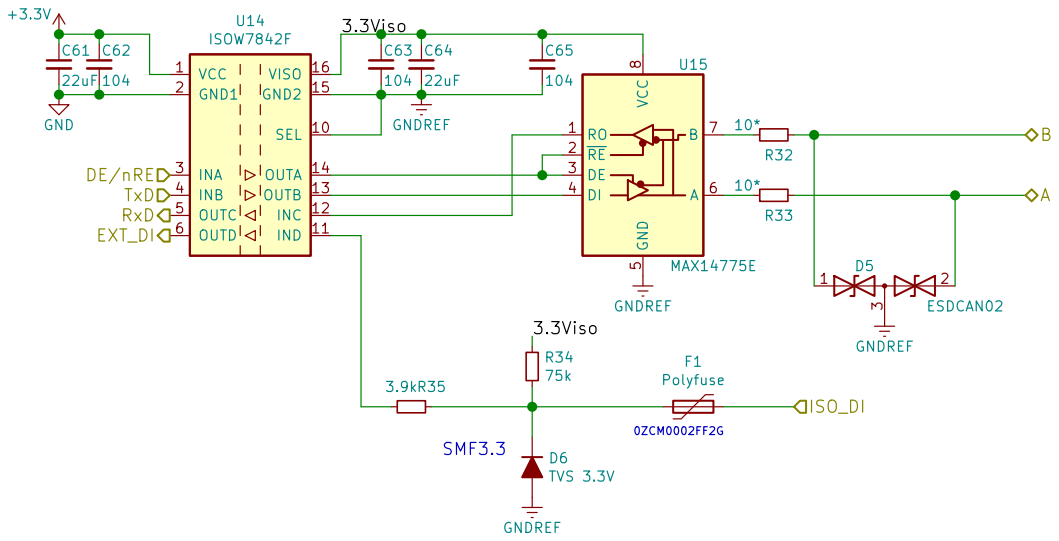
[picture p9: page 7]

Author: Tym Zhu
File: RS485.sch Sheet: /RS485/ Robotics & Mechanisms Labratory(RoMeLa) UCLA

Id: 7/7 Title: RoMeLa Motor Gen2

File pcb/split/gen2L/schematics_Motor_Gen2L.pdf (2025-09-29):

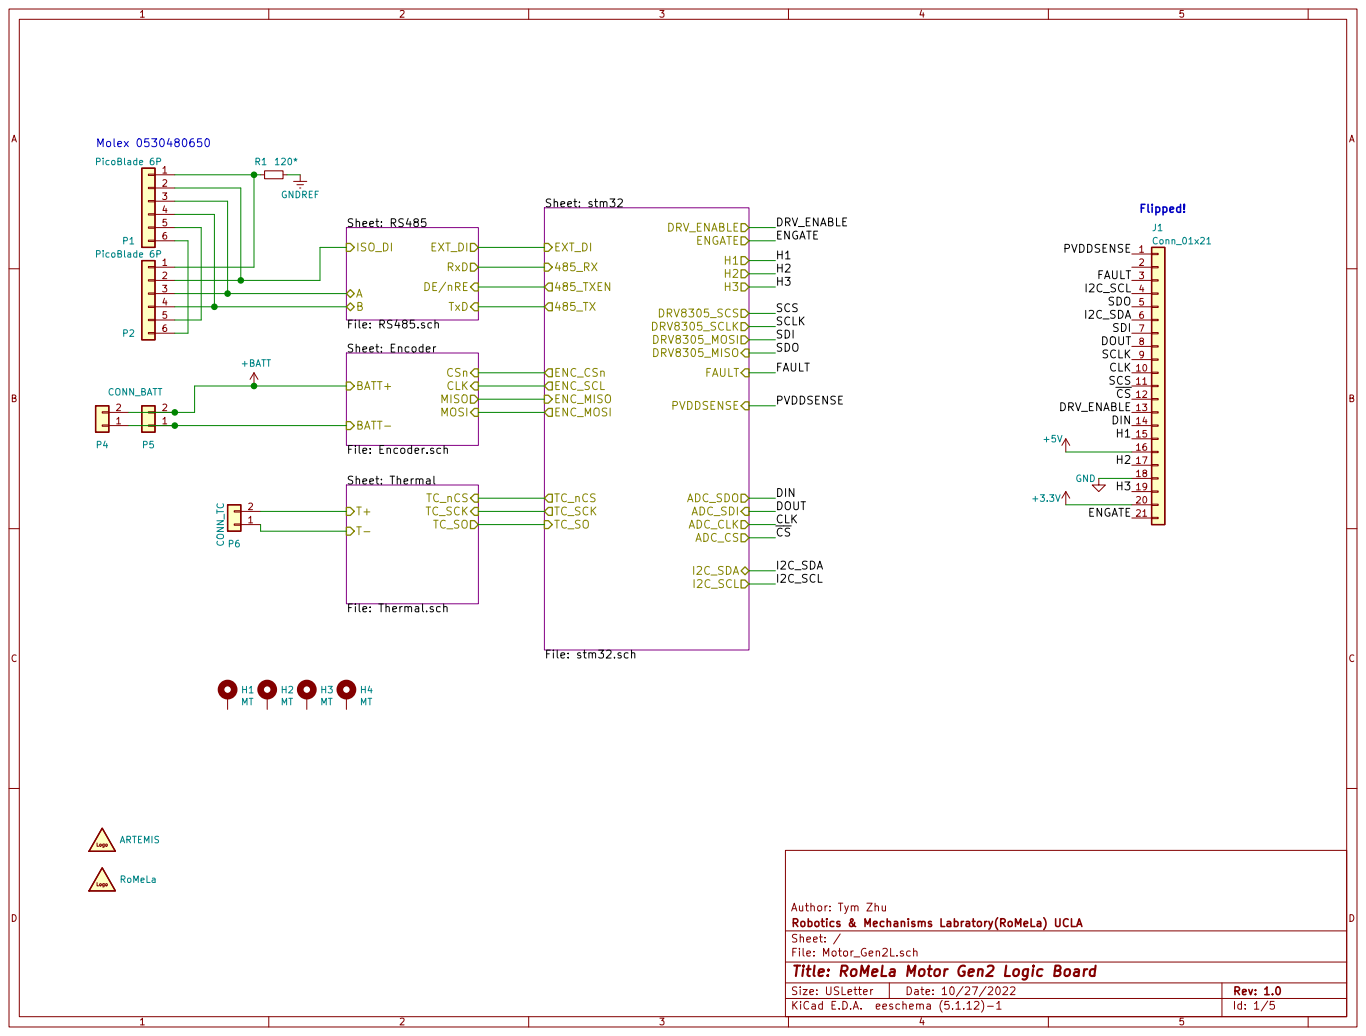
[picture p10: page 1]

Author: Tym Zhu
File: Motor_Gen2L.sch Sheet: / Robotics & Mechanisms Labratory(RoMeLa) UCLA

Id: 1/5 Title: RoMeLa Motor Gen2 Logic Board

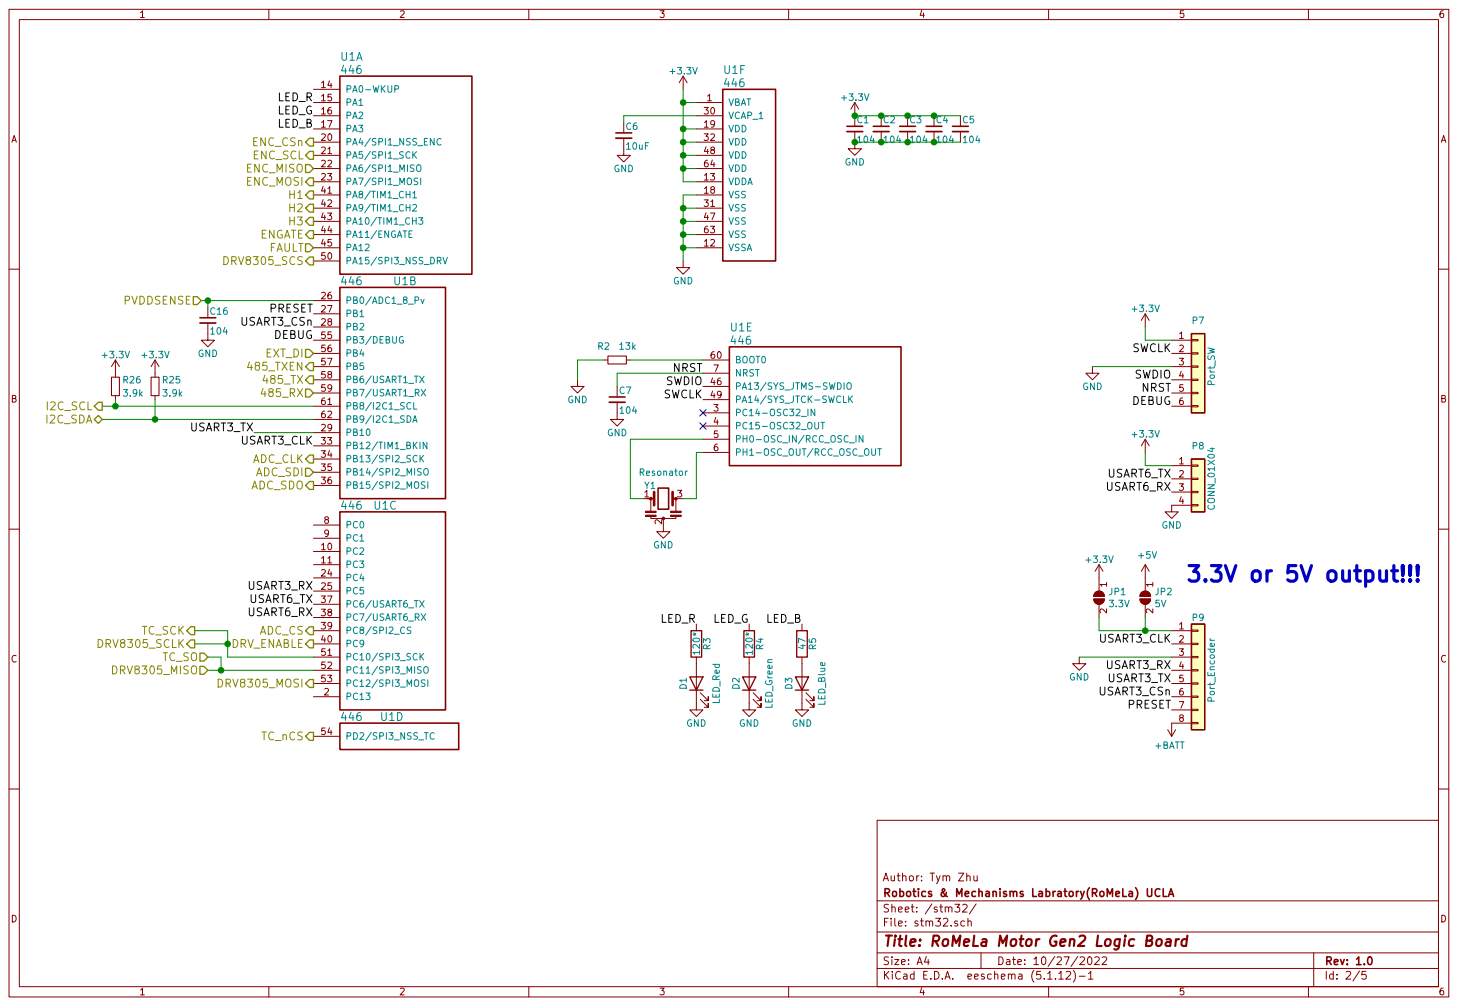
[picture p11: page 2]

File: stm32.sch Sheet: /stm32/ Robotics & Mechanisms Labratory(RoMeLa) UCLA

Id: 2/5 Title: RoMeLa Motor Gen2 Logic Board

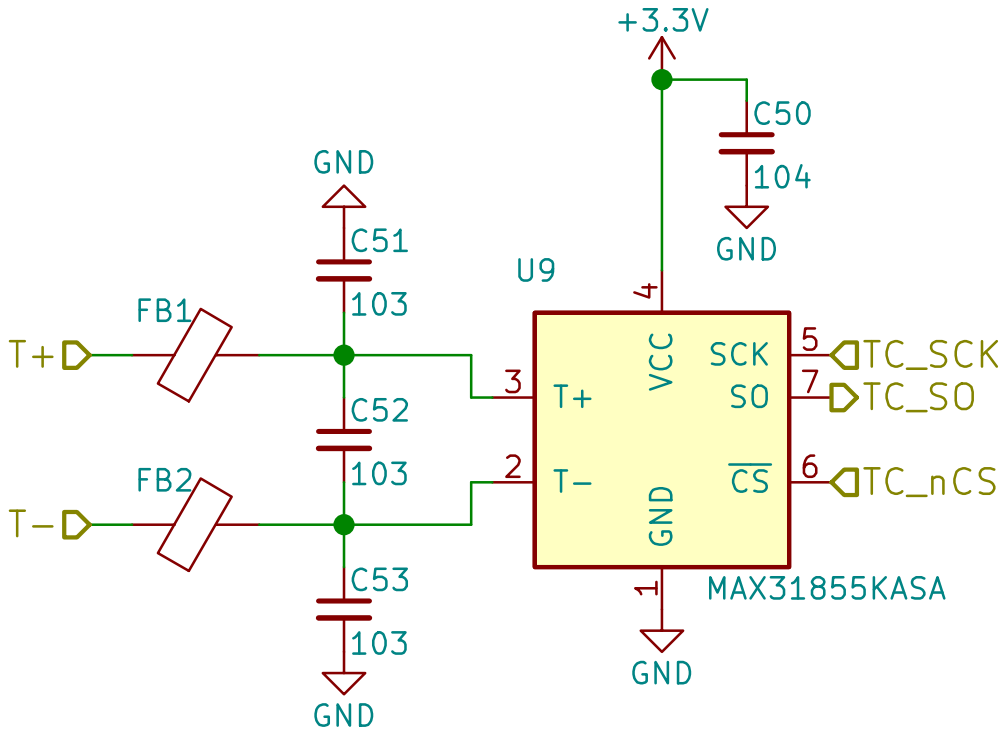
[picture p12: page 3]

Author: Tym Zhu
File: Thermal.sch Sheet: /Thermal/ Robotics & Mechanisms Labratory(RoMeLa) UCLA

Id: 3/5 Title: RoMeLa Motor Gen2 Logic Board

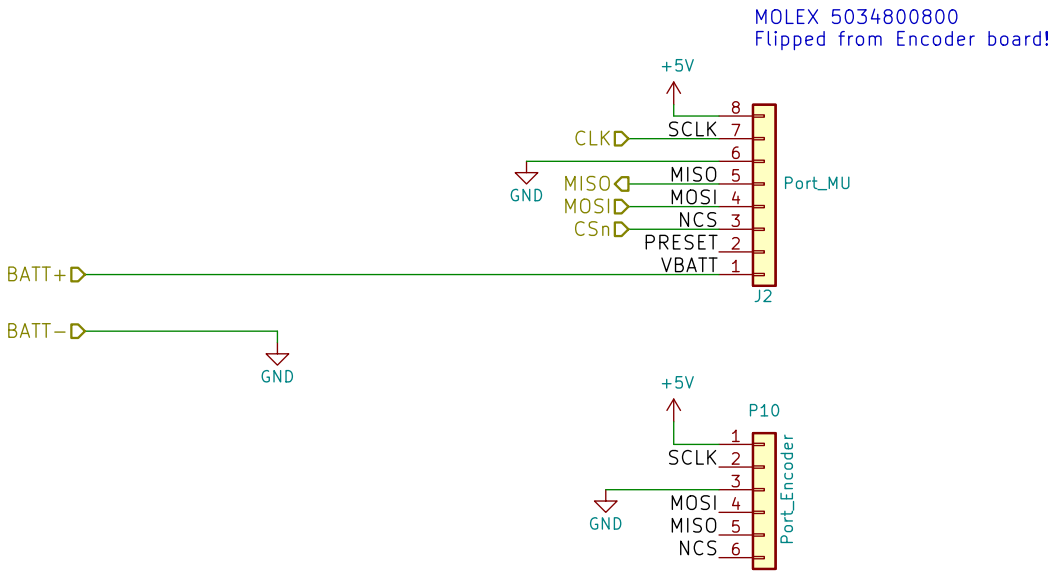
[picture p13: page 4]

MOLEX 5034800800
Flipped from Encoder board!
PRESET VBATT SCLK

File: Encoder.sch Sheet: /Encoder/ Robotics & Mechanisms Labratory(RoMeLa) UCLA

Id: 4/5 Title: RoMeLa Motor Gen2 Logic Board

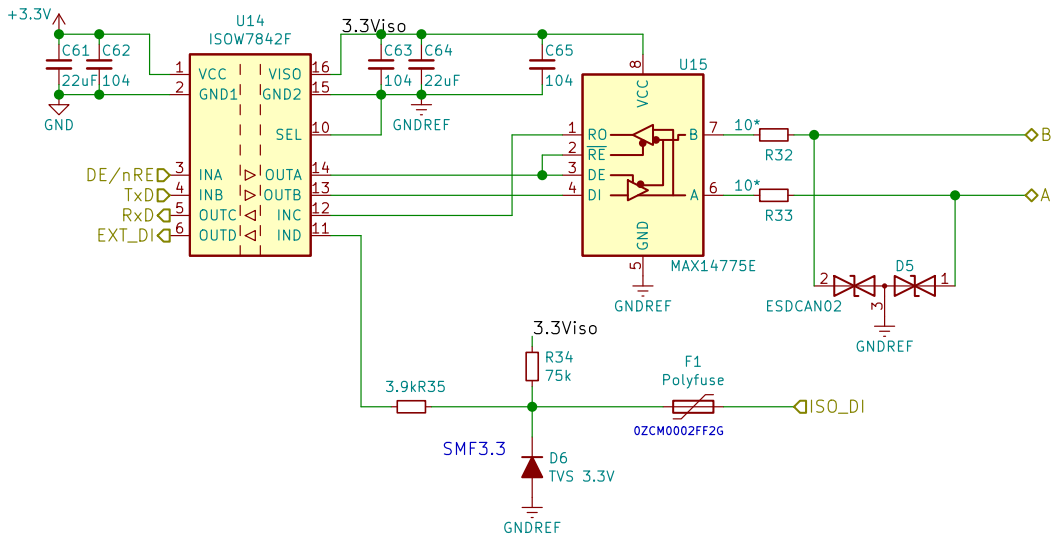
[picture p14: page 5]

Author: Tym Zhu
File: RS485.sch Sheet: /RS485/ Robotics & Mechanisms Labratory(RoMeLa) UCLA

Id: 5/5 Title: RoMeLa Motor Gen2 Logic Board

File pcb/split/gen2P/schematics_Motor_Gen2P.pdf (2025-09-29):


Sheet: Thermal File: Thermal.sch

Author: Tym Zhu
File: Motor_Gen2P.sch Sheet: / Robotics & Mechanisms Labratory(RoMeLa) UCLA

Id: 1/4 Title: RoMeLa Motor Gen2 Power Board


Author: Tym Zhu
Robotics & Mechanisms Labratory(RoMeLa) UCLA
Sheet: /Power_Stage/
File: Power_Stage.sch
Id: 2/4 Title: RoMeLa Motor Gen2 Power Board


7 SDI 8 CS 9 U7 ADS8353 GNDA GND GNDA

Changed to direct drive

Author: Tym Zhu
Robotics & Mechanisms Labratory(RoMeLa) UCLA
Sheet: /Current_ADC/
File: Current_ADC.sch
Id: 3/4 Title: RoMeLa Motor Gen2 Power Board


File: Thermal.sch Sheet: /Thermal/ Robotics & Mechanisms Labratory(RoMeLa) UCLA

Id: 4/4 Title: RoMeLa Motor Gen2 Power Board

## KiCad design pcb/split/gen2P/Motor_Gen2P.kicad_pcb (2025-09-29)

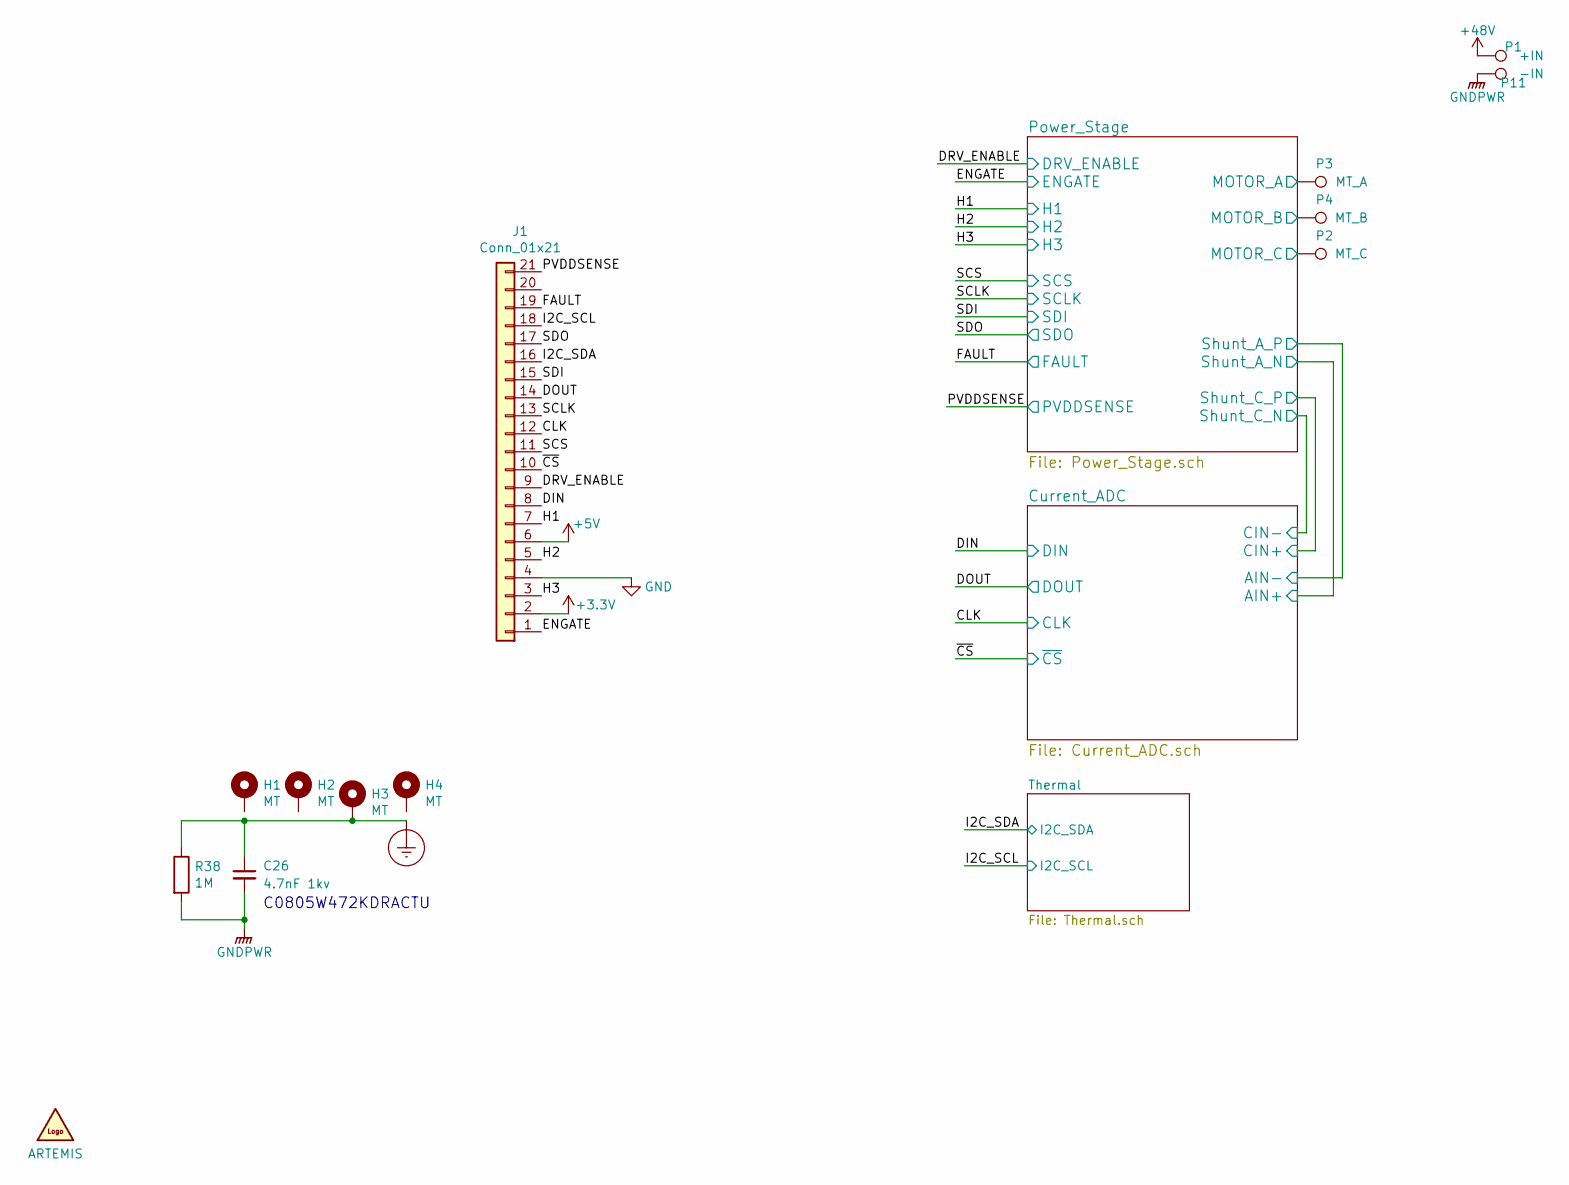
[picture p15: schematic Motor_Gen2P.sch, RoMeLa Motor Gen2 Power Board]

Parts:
C26: 4.7nF 1kv; C_0805_2012Metric
G1: ARTEMIS; artemis_logo_small
H1, H2, H3, H4: MT; MountingHole_2.7mm_M2.5_Pad_Via
J1: Conn_01x21; Molex_5019122190_2Rows-21Pins_P0.30mm
P1: +IN; Motor_winding_SMT
P2: MT_C; motor_winding_oval_3mm
P3: MT_A; motor_winding_oval_3mm
P4: MT_B; motor_winding_oval_3mm
P11: -IN; Motor_winding_SMT
R38: 1M; R_0805_2012Metric

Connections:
+3V3: J1.2; also elsewhere on the board
+5V: J1.6; also elsewhere on the board
+48V: P1.1; also elsewhere on the board
/CLK: J1.12; also elsewhere on the board
/DIN: J1.8; also elsewhere on the board
/DOUT: J1.14; also elsewhere on the board
/DRV_ENABLE: J1.9; also elsewhere on the board
/ENGATE: J1.1; also elsewhere on the board
/FAULT: J1.19; also elsewhere on the board
/H1: J1.7; also elsewhere on the board
/H2: J1.5; also elsewhere on the board
/H3: J1.3; also elsewhere on the board
/I2C_SCL: J1.18; also elsewhere on the board
/I2C_SDA: J1.16; also elsewhere on the board
/PVDDSENSE: J1.21; also elsewhere on the board
/Power_Stage/MOTOR_A: P3.1; also elsewhere on the board
/Power_Stage/MOTOR_B: P4.1; also elsewhere on the board
/Power_Stage/MOTOR_C: P2.1; also elsewhere on the board
/SCLK: J1.13; also elsewhere on the board
/SCS: J1.11; also elsewhere on the board
/SDI: J1.15; also elsewhere on the board
/SDO: J1.17; also elsewhere on the board
/~CS: J1.10; also elsewhere on the board
Earth_Protective: C26.1, H3.1, R38.1
GND: J1.4; also elsewhere on the board
GNDPWR: C26.2, P11.1, R38.2; also elsewhere on the board

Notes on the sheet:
C0805W472KDRACTU

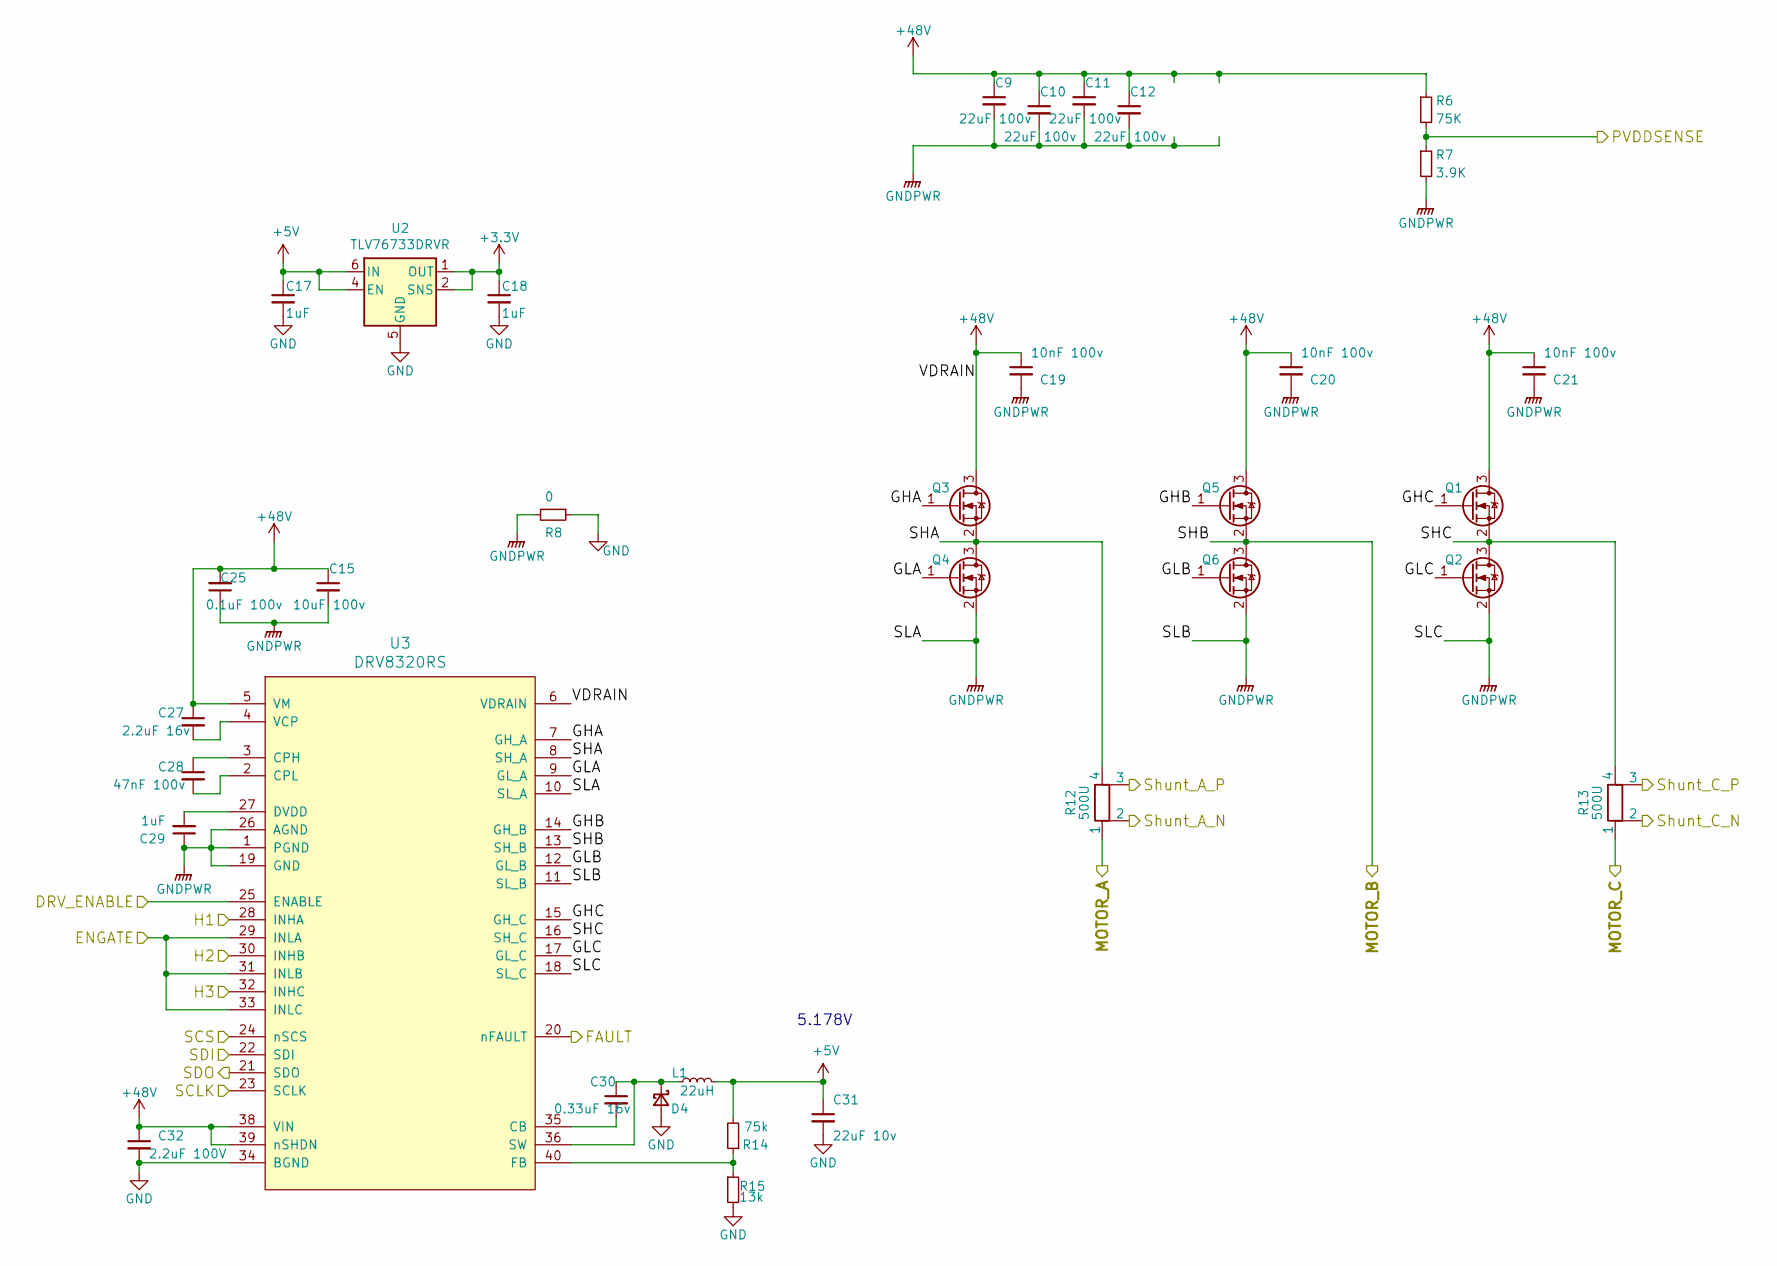
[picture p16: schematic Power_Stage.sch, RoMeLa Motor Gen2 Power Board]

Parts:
C9, C10, C11, C12: 22uF 100v; C_2220_5650Metric
C15: 10uF 100v; C_1210_3225Metric
C17, C18, C29: 1uF; C_0603_1608Metric
C19, C20, C21: 10nF 100v; C_0603_1608Metric
C25: 0.1uF 100v; C_0603_1608Metric
C27: 2.2uF 16v; C_0603_1608Metric
C28: 47nF 100v; C_0603_1608Metric
C30: 0.33uF 16v; C_0603_1608Metric
C31: 22uF 10v; C_1206_3216Metric
C32: 2.2uF 100V; C_1206_3216Metric
D4: D_Schottky_Small; D_TUMD2
L1: 22uH; L_Taiyo-Yuden_DND4040WK
Q1, Q2, Q3, Q4, Q5, Q6: NMOS; DFNW8_8.3x8.4_short
R6: 75K; R_0402_1005Metric
R7: 3.9K; R_0402_1005Metric
R8: 0; NetTie-2_SMD_Pad0.5mm
R12, R13: 500U; RES_W1612_4Terminal
R14: 75k; R_0402_1005Metric
R15: 13k; R_0402_1005Metric
U2: TLV76733DRVR; WSON-6-1EP_2x2mm_P0.65mm_EP1x1.6mm
U3: DRV8320RS; Texas_S-PVQFN-N40_EP4.15x4.15mm

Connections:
+3V3: C18.1, U2.1 (OUT), U2.2 (SNS); also elsewhere on the board
+5V: C17.1, C31.1, L1.2, R14.2, U2.4 (EN), U2.6 (IN); also elsewhere on the board
+48V: C9.1, C10.1, C11.1, C12.1, C15.1, C19.1, C20.1, C21.1, C25.2, C27.1, C32.1, Q1.3 (D), Q3.3 (D), Q5.3 (D), R6.1, U3.5 (VM), U3.6 (VDRAIN), U3.38 (VIN), U3.39 (nSHDN); also elsewhere on the board
/Current_ADC/AIN+: R12.2; also elsewhere on the board
/Current_ADC/AIN-: R12.3; also elsewhere on the board
/Current_ADC/CIN+: R13.3; also elsewhere on the board
/Current_ADC/CIN-: R13.2; also elsewhere on the board
/DRV_ENABLE: U3.25 (ENABLE); also elsewhere on the board
/ENGATE: U3.29 (INLA), U3.31 (INLB), U3.33 (INLC); also elsewhere on the board
/FAULT: U3.20 (nFAULT); also elsewhere on the board
/H1: U3.28 (INHA); also elsewhere on the board
/H2: U3.30 (INHB); also elsewhere on the board
/H3: U3.32 (INHC); also elsewhere on the board
/PVDDSENSE: R6.2, R7.1; also elsewhere on the board
/Power_Stage/GHA: Q3.1 (G), U3.7 (GH_A)
/Power_Stage/GHB: Q5.1 (G), U3.14 (GH_B)
/Power_Stage/GHC: Q1.1 (G), U3.15 (GH_C)
/Power_Stage/GLA: Q4.1 (G), U3.9 (GL_A)
/Power_Stage/GLB: Q6.1 (G), U3.12 (GL_B)
/Power_Stage/GLC: Q2.1 (G), U3.17 (GL_C)
/Power_Stage/MOTOR_A: R12.1; also elsewhere on the board
/Power_Stage/MOTOR_B: Q5.2 (S), Q6.3 (D), U3.13 (SH_B); also elsewhere on the board
/Power_Stage/MOTOR_C: R13.1; also elsewhere on the board
/Power_Stage/SHA: Q3.2 (S), Q4.3 (D), R12.4, U3.8 (SH_A)
/Power_Stage/SHC: Q1.2 (S), Q2.3 (D), R13.4, U3.16 (SH_C)
/SCLK: U3.23 (SCLK); also elsewhere on the board
/SCS: U3.24 (nSCS); also elsewhere on the board
/SDI: U3.22 (SDI); also elsewhere on the board
/SDO: U3.21 (SDO); also elsewhere on the board
GND: C17.2, C18.2, C31.2, C32.2, D4.2 (A), R8.1, R15.2, U2.3 (GND), U2.5 (GND), U2.7 (GND), U3.34 (BGND); also elsewhere on the board
GNDPWR: C9.2, C10.2, C11.2, C12.2, C15.2, C19.2, C20.2, C21.2, C25.1, C29.1, Q2.2 (S), Q4.2 (S), Q6.2 (S), R7.2, R8.2, U3.1 (PGND), U3.10 (SL_A), U3.11 (SL_B), U3.18 (SL_C), U3.19 (GND), U3.26 (AGND), U3.41 (PAD); also elsewhere on the board
unnamed: C27.2, U3.4 (VCP)
unnamed: C28.1, U3.3 (CPH)
unnamed: C28.2, U3.2 (CPL)
unnamed: C29.2, U3.27 (DVDD)
unnamed: C30.1, D4.1 (K), L1.1, U3.36 (SW)
unnamed: C30.2, U3.35 (CB)
unnamed: R14.1, R15.1, U3.40 (FB)

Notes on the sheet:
5.178V

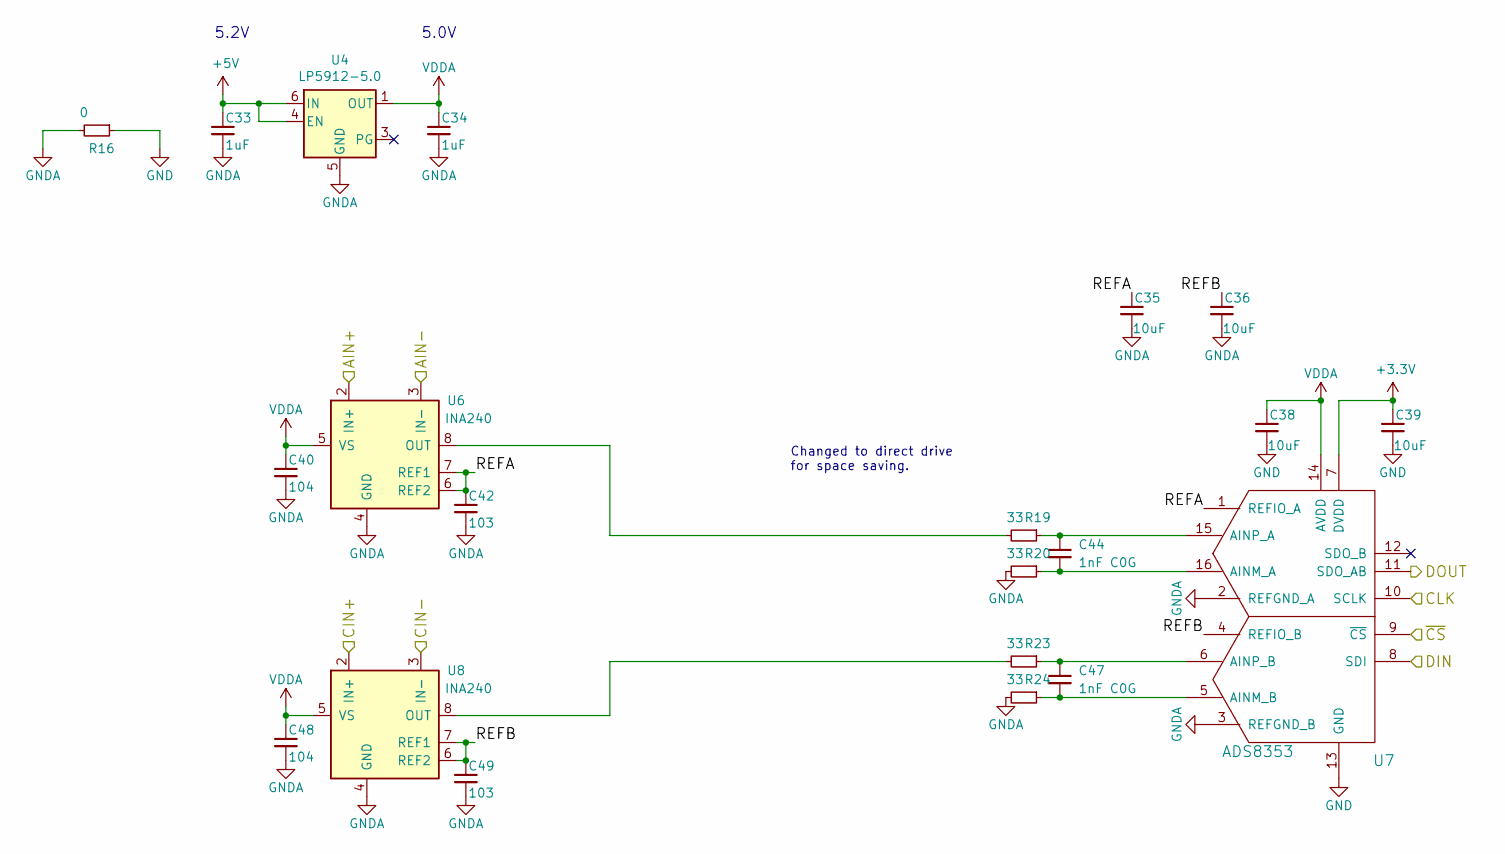
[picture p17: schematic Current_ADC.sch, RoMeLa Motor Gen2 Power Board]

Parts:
C33, C34: 1uF; C_0603_1608Metric
C35, C36, C38, C39: 10uF; C_0805_2012Metric
C40, C48: 104; C_0402_1005Metric
C42, C49: 103; C_0402_1005Metric
C44, C47: 1nF C0G; C_0402_1005Metric
R16: 0; NetTie-2_SMD_Pad0.5mm
R19, R20, R23, R24: 33; R_0402_1005Metric
U4: LP5912-5.0; WSON-6-1EP_2x2mm_P0.65mm_EP1x1.6mm
U6, U8: INA240; TSSOP-8_4.4x3mm_P0.65mm
U7: ADS8353; WQFN-16-1EP_3x3mm_P0.5mm_EP0.8x0.8mm

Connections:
+3V3: C39.1, U7.7 (DVDD); also elsewhere on the board
+5V: C33.1, U4.4 (EN), U4.6 (IN); also elsewhere on the board
/CLK: U7.10 (SCLK); also elsewhere on the board
/Current_ADC/AIN+: U6.2 (IN+); also elsewhere on the board
/Current_ADC/AIN-: U6.3 (IN-); also elsewhere on the board
/Current_ADC/CIN+: U8.2 (IN+); also elsewhere on the board
/Current_ADC/CIN-: U8.3 (IN-); also elsewhere on the board
/Current_ADC/REFA: C35.1, C42.1, U6.6 (REF2), U6.7 (REF1), U7.1 (REFIO_A)
/Current_ADC/REFB: C36.1, C49.1, U7.4 (REFIO_B), U8.6 (REF2), U8.7 (REF1)
/DIN: U7.8 (SDI); also elsewhere on the board
/DOUT: U7.11 (SDO_AB); also elsewhere on the board
/~CS: U7.9 (~CS); also elsewhere on the board
GND: C38.2, C39.2, R16.1, U7.13 (GND), U7.17 (Pad); also elsewhere on the board
GNDA: C33.2, C34.2, C35.2, C36.2, C40.2, C42.2, C48.2, C49.2, R16.2, R20.2, R24.2, U4.5 (GND), U4.7 (GND), U6.4 (GND), U7.2 (REFGND_A), U7.3 (REFGND_B), U8.4 (GND)
unnamed: C44.1, R19.1, U7.15 (AINP_A)
unnamed: C44.2, R20.1, U7.16 (AINM_A)
unnamed: C47.1, R23.1, U7.6 (AINP_B)
unnamed: C47.2, R24.1, U7.5 (AINM_B)
unnamed: R19.2, U6.8 (OUT)
unnamed: R23.2, U8.8 (OUT)
VDDA: C34.1, C38.1, C40.1, C48.1, U4.1 (OUT), U6.5 (VS), U7.14 (AVDD), U8.5 (VS)

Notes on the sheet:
5.2V
5.0V
Changed to direct drive for space saving.

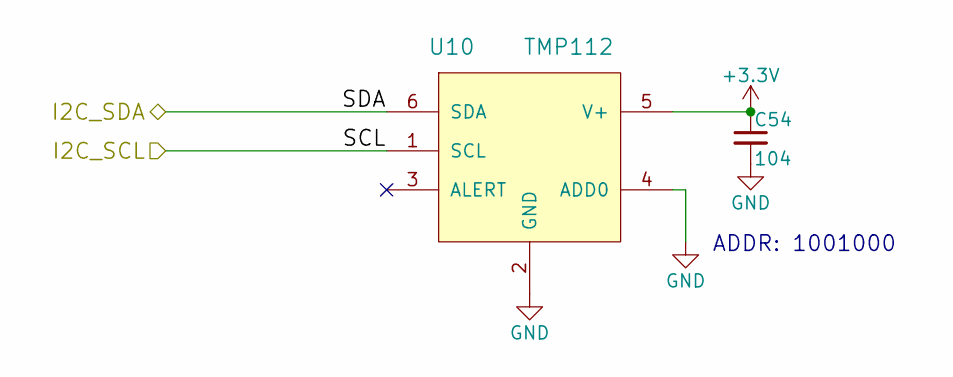
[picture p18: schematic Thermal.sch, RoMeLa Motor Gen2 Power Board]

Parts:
C54: 104; C_0402_1005Metric
U10: TMP112; SOT-563

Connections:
+3V3: C54.1, U10.5 (V+); also elsewhere on the board
/I2C_SCL: U10.1 (SCL); also elsewhere on the board
/I2C_SDA: U10.6 (SDA); also elsewhere on the board
GND: C54.2, U10.2 (GND), U10.4 (ADD0); also elsewhere on the board

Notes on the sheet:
ADDR: 1001000

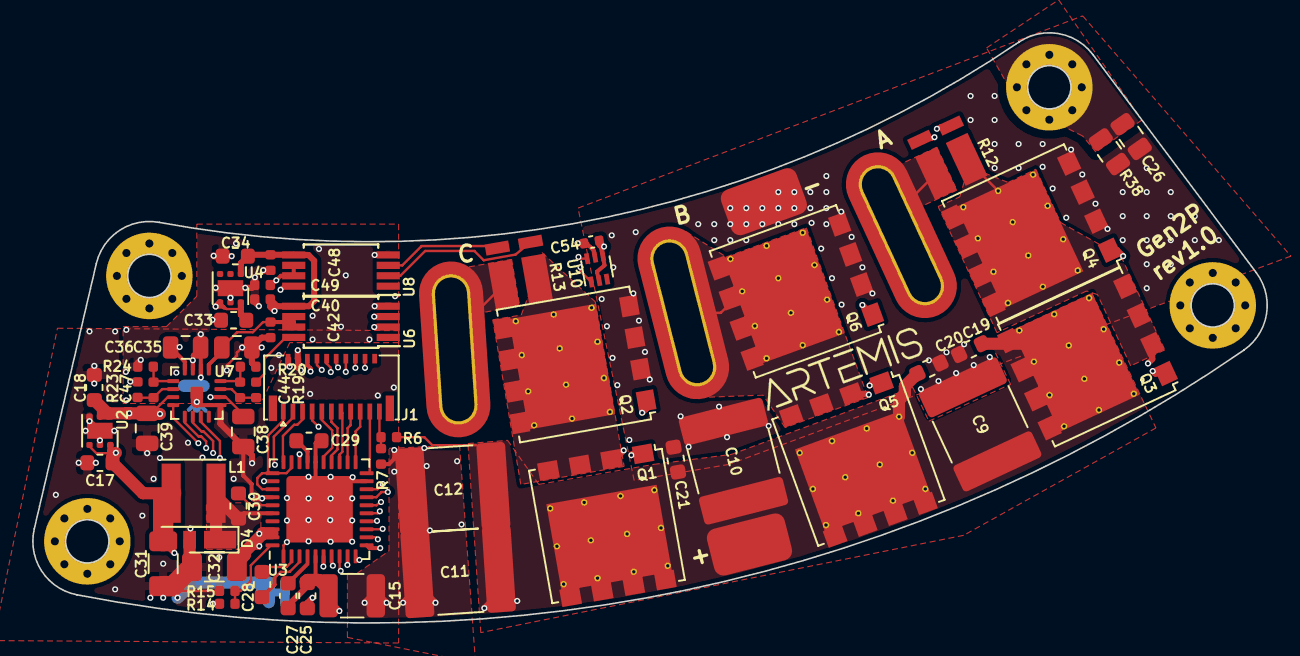
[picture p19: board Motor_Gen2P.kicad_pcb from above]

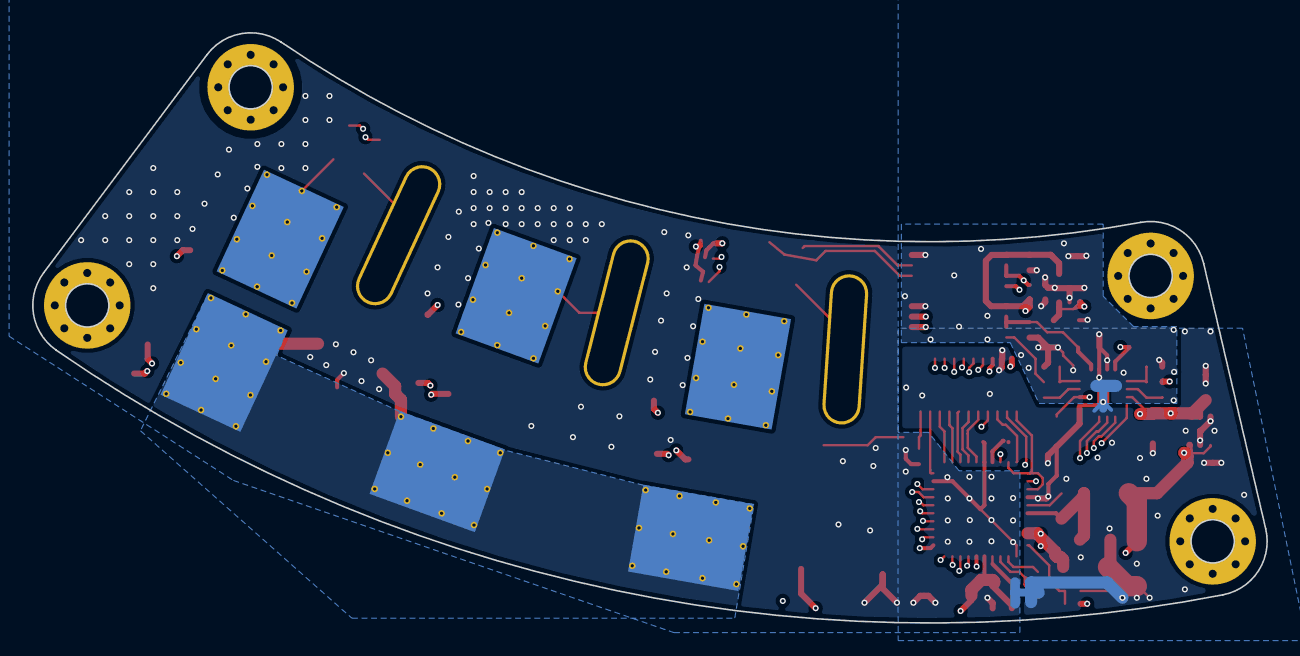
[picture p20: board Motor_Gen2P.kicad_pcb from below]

Board: 4 copper layers, 77.1 x 36.8 mm, 70 parts (2 on the bottom side), 55 nets.

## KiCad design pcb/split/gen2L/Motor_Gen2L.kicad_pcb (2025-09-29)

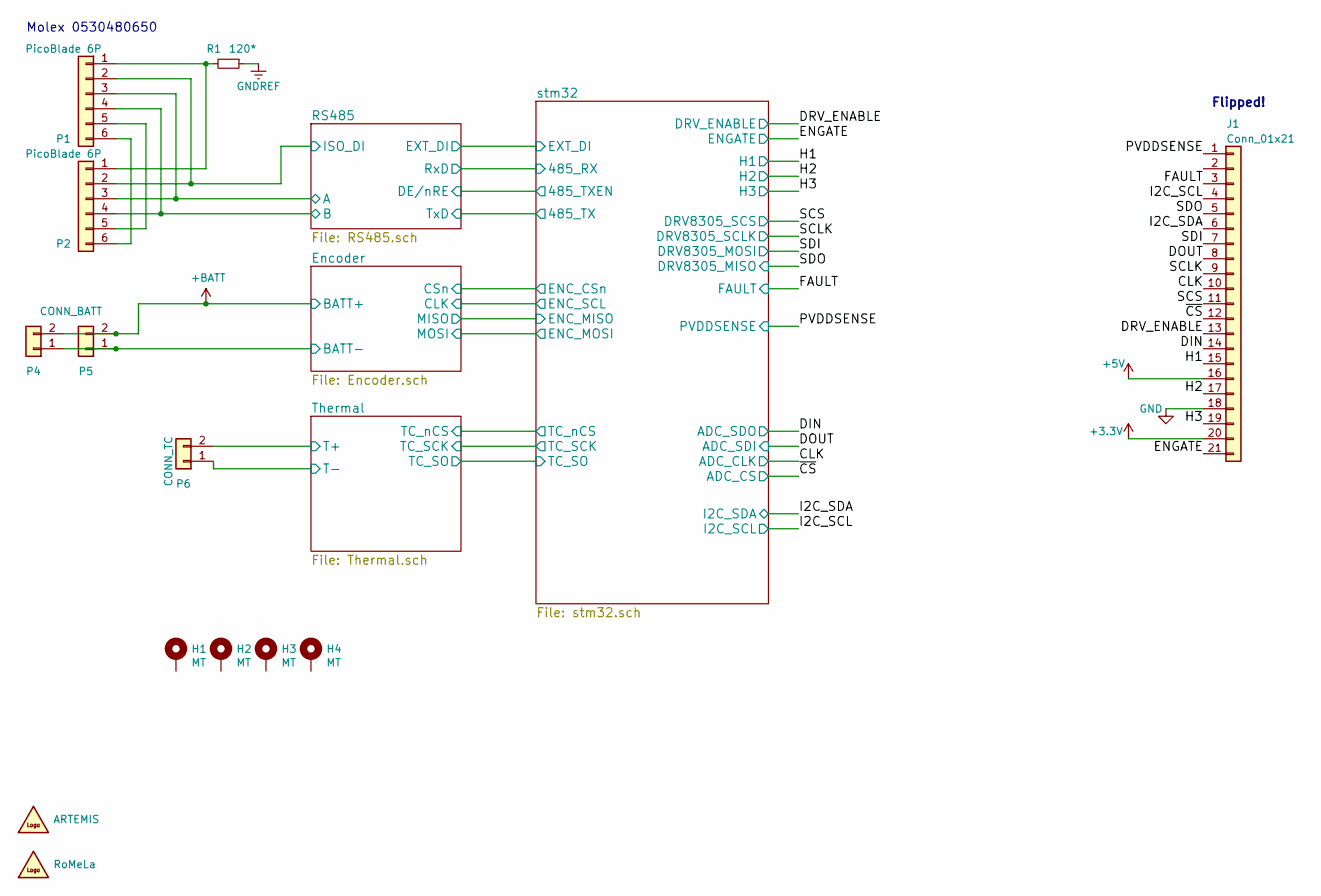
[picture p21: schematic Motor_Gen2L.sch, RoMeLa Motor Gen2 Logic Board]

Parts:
G1: ARTEMIS; artemis_logo_small
G2: RoMeLa; LOGO
H1, H2, H3, H4: MT; MountingHole_2.7mm_M2.5_Pad_Via
J1: Conn_01x21; Molex_5019122190_2Rows-21Pins_P0.30mm
P1, P2: PicoBlade 6P; Molex_PicoBlade_53048-0650_1x06_P1.25mm_Horizontal
P4, P5: CONN_BATT; Molex_PicoBlade_53048-0210_1x02_P1.25mm_Horizontal
P6: CONN_TC; JST_SH_SM02B-SRSS-TB_1x02-1MP_P1.00mm_Horizontal
R1: 120*; R_0603_1608Metric

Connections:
+3V3: J1.20; also elsewhere on the board
+5V: J1.16; also elsewhere on the board
+BATT: P4.2, P5.2; also elsewhere on the board
/CLK: J1.10; also elsewhere on the board
/DIN: J1.14; also elsewhere on the board
/DOUT: J1.8; also elsewhere on the board
/DRV_ENABLE: J1.13; also elsewhere on the board
/ENGATE: J1.21; also elsewhere on the board
/FAULT: J1.3; also elsewhere on the board
/H1: J1.15; also elsewhere on the board
/H2: J1.17; also elsewhere on the board
/H3: J1.19; also elsewhere on the board
/I2C_SCL: J1.4; also elsewhere on the board
/I2C_SDA: J1.6; also elsewhere on the board
/PVDDSENSE: J1.1; also elsewhere on the board
/RS485/A: P1.3, P2.3; also elsewhere on the board
/RS485/B: P1.4, P2.4; also elsewhere on the board
/RS485/ISO_DI: P1.2, P2.2; also elsewhere on the board
/SCLK: J1.9; also elsewhere on the board
/SCS: J1.11; also elsewhere on the board
/SDI: J1.7; also elsewhere on the board
/SDO: J1.5; also elsewhere on the board
/Thermal/T+: P6.2; also elsewhere on the board
/Thermal/T-: P6.1; also elsewhere on the board
/~CS: J1.12; also elsewhere on the board
GND: J1.18, P4.1, P5.1; also elsewhere on the board
GNDREF: R1.1; also elsewhere on the board
unnamed: P1.1, P2.1, R1.2
unnamed: P1.5, P2.5
unnamed: P1.6, P2.6

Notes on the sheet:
Molex 0530480650
Flipped!

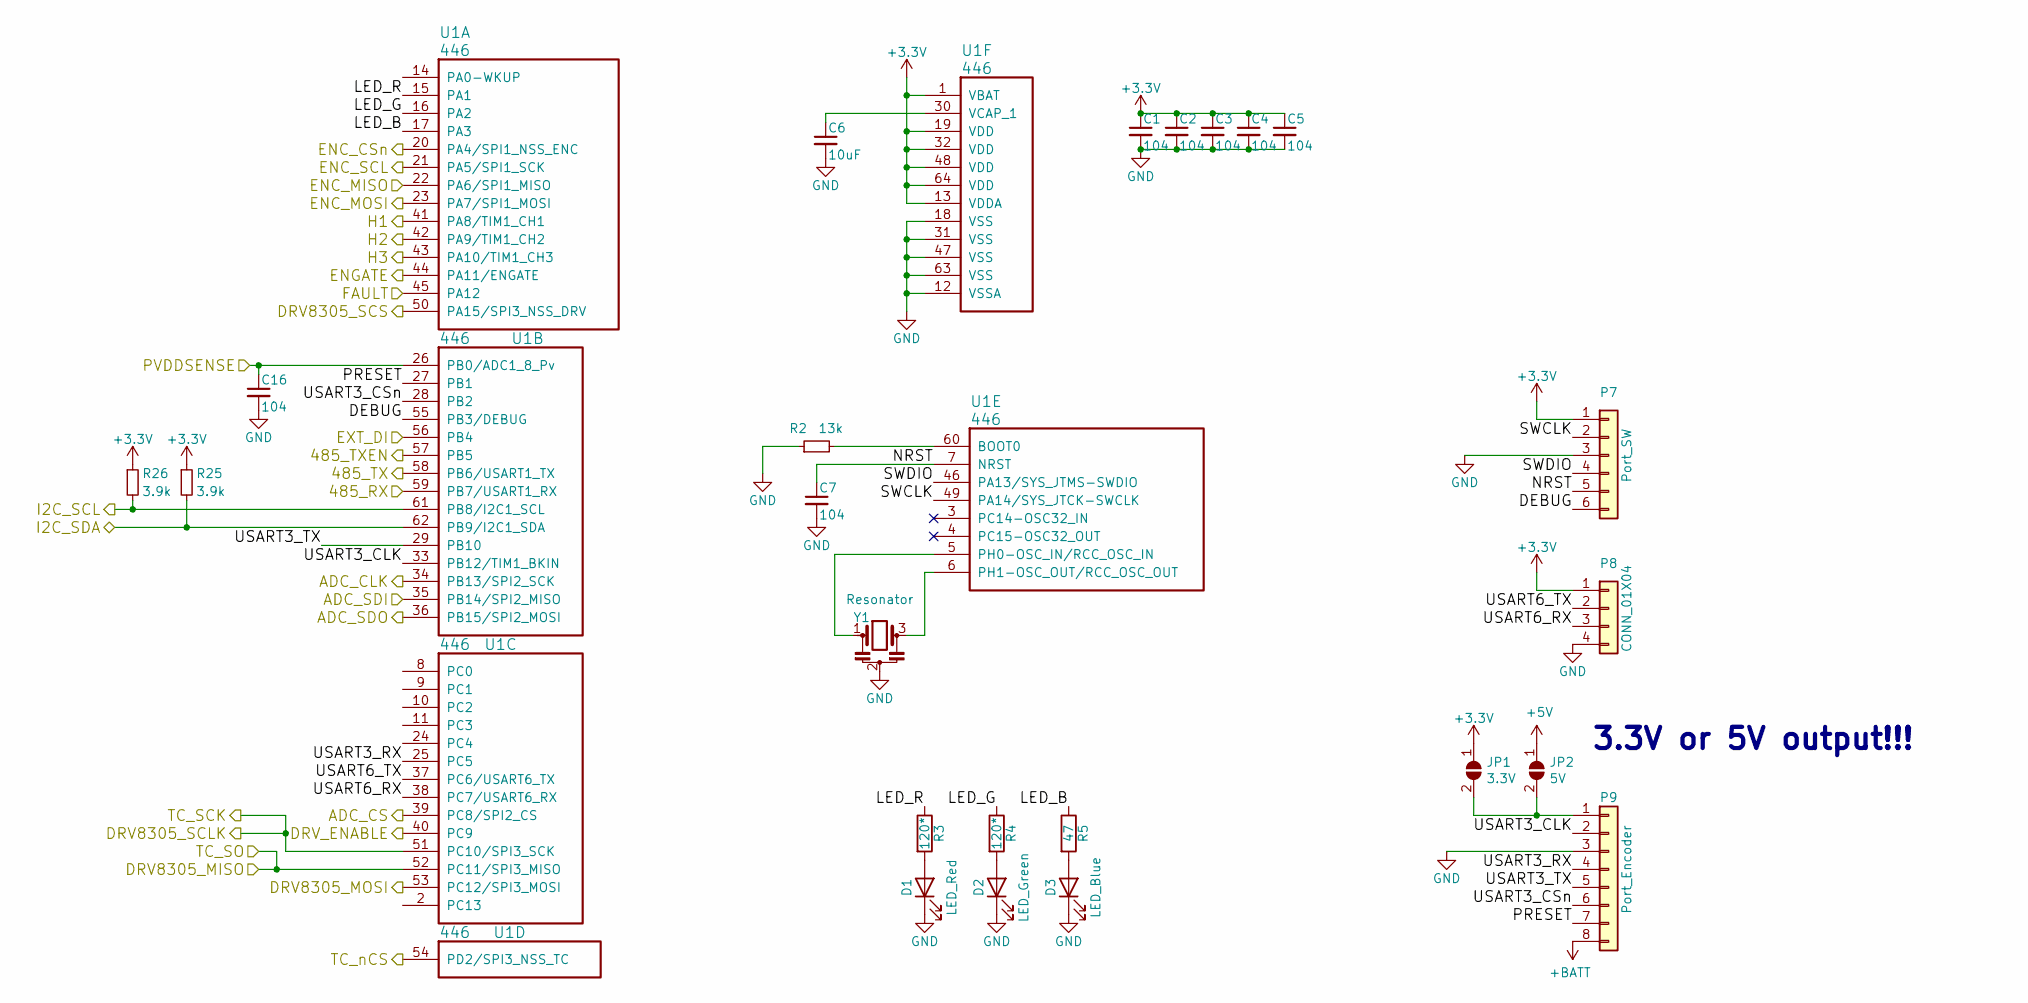
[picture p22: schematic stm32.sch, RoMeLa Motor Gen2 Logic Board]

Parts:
C1, C2, C3, C4, C5, C7, C16: 104; C_0402_1005Metric
C6: 10uF; C_0805_2012Metric
D1: LED_Red; LED_0603_1608Metric
D2: LED_Green; LED_0603_1608Metric
D3: LED_Blue; LED_0603_1608Metric
JP1: 3.3V; SolderJumper_Open_TrianglePad
JP2: 5V; SolderJumper_Open_TrianglePad
P7: Port_SW; JST_SH_BM06B-SRSS-TB_1x06-1MP_P1.00mm_Vertical
P8: CONN_01X04; JST_SH_BM04B-SRSS-TB_1x04-1MP_P1.00mm_Vertical
P9: Port_Encoder; FFC_8POS_0.5mm_BackFlip
R2: 13k; R_0402_1005Metric
R3, R4: 120*; R_0603_1608Metric
R5: 47; R_0603_1608Metric
R25, R26: 3.9k; R_0402_1005Metric
U1: 446; LQFP-64_10x10mm_P0.5mm
Y1: Resonator; Resonator_3.2x1.3

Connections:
+3V3: C1.1, C2.1, C3.1, C4.1, C5.1, JP1.1 (A), P7.1, P8.1, R25.1, R26.1, U1.1 (VBAT), U1.13 (VDDA), U1.19 (VDD), U1.32 (VDD), U1.48 (VDD), U1.64 (VDD); also elsewhere on the board
+5V: JP2.1 (A); also elsewhere on the board
+BATT: P9.8; also elsewhere on the board
/CLK: U1.34 (PB13/SPI2_SCK); also elsewhere on the board
/DIN: U1.36 (PB15/SPI2_MOSI); also elsewhere on the board
/DOUT: U1.35 (PB14/SPI2_MISO); also elsewhere on the board
/DRV_ENABLE: U1.40 (PC9); also elsewhere on the board
/ENGATE: U1.44 (PA11/ENGATE); also elsewhere on the board
/Encoder/CLK: U1.21 (PA5/SPI1_SCK); also elsewhere on the board
/Encoder/CSn: U1.20 (PA4/SPI1_NSS_ENC); also elsewhere on the board
/FAULT: U1.45 (PA12); also elsewhere on the board
/H1: U1.41 (PA8/TIM1_CH1); also elsewhere on the board
/H2: U1.42 (PA9/TIM1_CH2); also elsewhere on the board
/H3: U1.43 (PA10/TIM1_CH3); also elsewhere on the board
/I2C_SCL: R26.2, U1.61 (PB8/I2C1_SCL); also elsewhere on the board
/I2C_SDA: R25.2, U1.62 (PB9/I2C1_SDA); also elsewhere on the board
/PVDDSENSE: C16.1, U1.26 (PB0/ADC1_8_Pv); also elsewhere on the board
/RS485/EXT_DI: U1.56 (PB4); also elsewhere on the board
/SCLK: U1.51 (PC10/SPI3_SCK); also elsewhere on the board
/SCS: U1.50 (PA15/SPI3_NSS_DRV); also elsewhere on the board
/SDI: U1.53 (PC12/SPI3_MOSI); also elsewhere on the board
/SDO: U1.52 (PC11/SPI3_MISO); also elsewhere on the board
/Thermal/TC_nCS: U1.54 (PD2/SPI3_NSS_TC); also elsewhere on the board
/stm32/485_RX: U1.59 (PB7/USART1_RX); also elsewhere on the board
/stm32/485_TX: U1.58 (PB6/USART1_TX); also elsewhere on the board
/stm32/485_TXEN: U1.57 (PB5); also elsewhere on the board
/stm32/DEBUG: P7.6, U1.55 (PB3/DEBUG)
/stm32/ENC_MISO: U1.22 (PA6/SPI1_MISO); also elsewhere on the board
/stm32/ENC_MOSI: U1.23 (PA7/SPI1_MOSI); also elsewhere on the board
/stm32/LED_B: R5.1, U1.17 (PA3)
/stm32/LED_G: R4.1, U1.16 (PA2)
/stm32/LED_R: R3.1, U1.15 (PA1)
/stm32/NRST: C7.1, P7.5, U1.7 (NRST)
/stm32/PRESET: P9.7, U1.27 (PB1)
/stm32/SWCLK: P7.2, U1.49 (PA14/SYS_JTCK-SWCLK)
/stm32/SWDIO: P7.4, U1.46 (PA13/SYS_JTMS-SWDIO)
/stm32/USART3_CLK: P9.2, U1.33 (PB12/TIM1_BKIN)
/stm32/USART3_CSn: P9.6, U1.28 (PB2)
/stm32/USART3_RX: P9.4, U1.25 (PC5)
/stm32/USART3_TX: P9.5, U1.29 (PB10)
/stm32/USART6_RX: P8.3, U1.38 (PC7/USART6_RX)
/stm32/USART6_TX: P8.2, U1.37 (PC6/USART6_TX)
/~CS: U1.39 (PC8/SPI2_CS); also elsewhere on the board
GND: C1.2, C2.2, C3.2, C4.2, C5.2, C6.2, C7.2, C16.2, D1.1 (K), D2.1 (K), D3.1 (K), P7.3, P8.4, P9.3, R2.1, U1.12 (VSSA), U1.18 (VSS), U1.31 (VSS), U1.47 (VSS), U1.63 (VSS), Y1.2; also elsewhere on the board
unnamed: C6.1, U1.30 (VCAP_1)
unnamed: D1.2 (A), R3.2
unnamed: D2.2 (A), R4.2
unnamed: D3.2 (A), R5.2
unnamed: JP1.2 (B), JP2.2 (B), P9.1
unnamed: R2.2, U1.60 (BOOT0)
unnamed: U1.5 (PH0-OSC_IN/RCC_OSC_IN), Y1.1
unnamed: U1.6 (PH1-OSC_OUT/RCC_OSC_OUT), Y1.3

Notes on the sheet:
3.3V or 5V output!!!

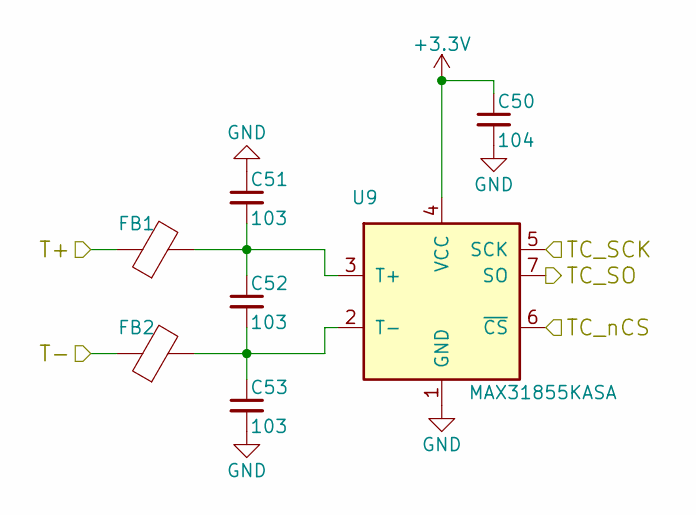
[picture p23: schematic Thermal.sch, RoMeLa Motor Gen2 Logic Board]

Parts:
C50: 104; C_0402_1005Metric
C51, C52, C53: 103; C_0402_1005Metric
FB1, FB2: Ferrite_Bead; R_0402_1005Metric
U9: MAX31855KASA; SOIC-8_3.9x4.9mm_P1.27mm

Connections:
+3V3: C50.1, U9.4 (VCC); also elsewhere on the board
/SCLK: U9.5 (SCK); also elsewhere on the board
/SDO: U9.7 (SO); also elsewhere on the board
/Thermal/T+: FB1.1; also elsewhere on the board
/Thermal/T-: FB2.1; also elsewhere on the board
/Thermal/TC_nCS: U9.6 (~CS~); also elsewhere on the board
GND: C50.2, C51.1, C53.2, U9.1 (GND); also elsewhere on the board
unnamed: C51.2, C52.1, FB1.2, U9.3 (T+)
unnamed: C52.2, C53.1, FB2.2, U9.2 (T-)

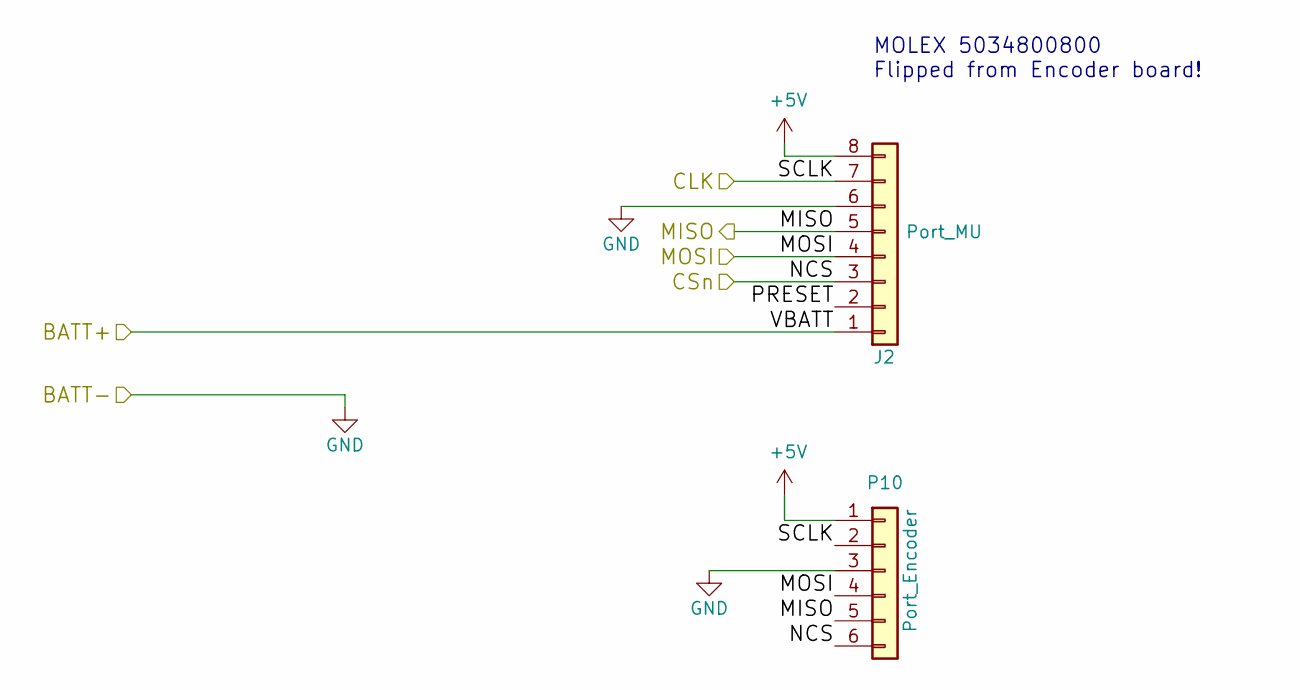
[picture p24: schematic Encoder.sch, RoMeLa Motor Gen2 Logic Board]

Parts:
J2: Port_MU; FFC_8POS_0.5mm_BackFlip
P10: Port_Encoder; JST_SH_BM06B-SRSS-TB_1x06-1MP_P1.00mm_Vertical

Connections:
+5V: J2.8, P10.1; also elsewhere on the board
+BATT: J2.1; also elsewhere on the board
/Encoder/CLK: J2.7, P10.2; also elsewhere on the board
/Encoder/CSn: J2.3, P10.6; also elsewhere on the board
/Encoder/PRESET: J2.2
/stm32/ENC_MISO: J2.5, P10.5; also elsewhere on the board
/stm32/ENC_MOSI: J2.4, P10.4; also elsewhere on the board
GND: J2.6, P10.3; also elsewhere on the board

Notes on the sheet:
MOLEX 5034800800 Flipped from Encoder board!

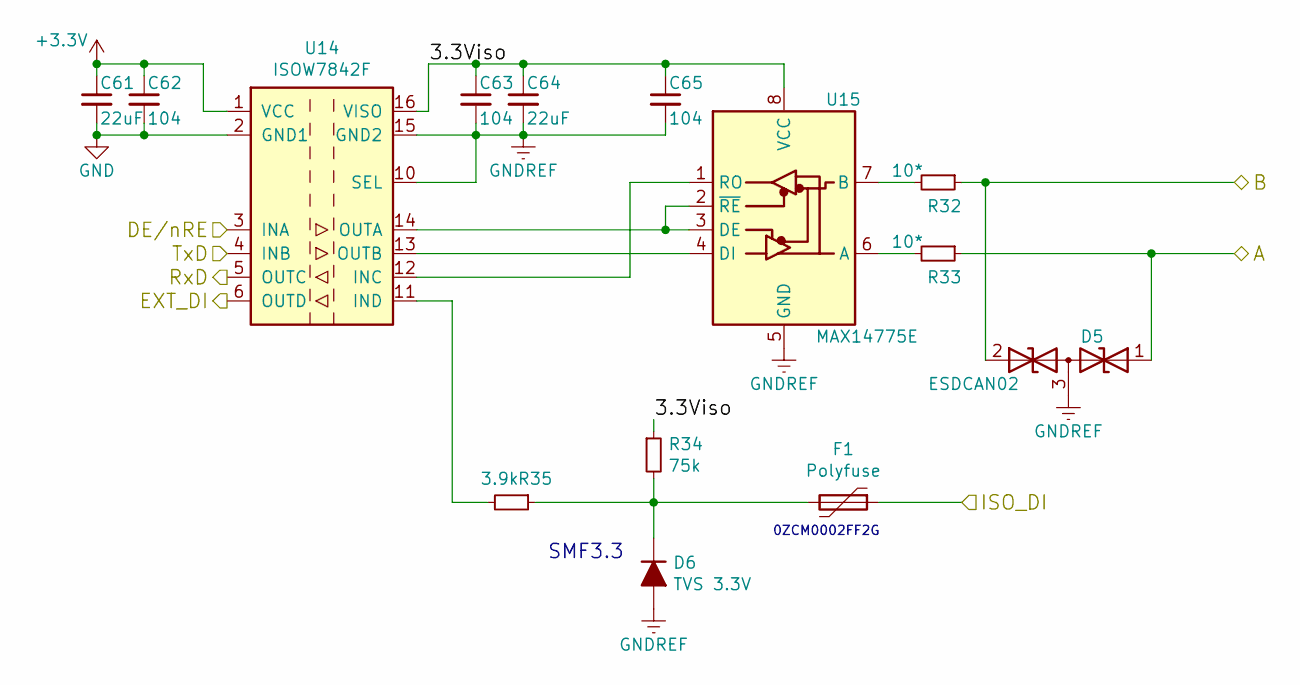
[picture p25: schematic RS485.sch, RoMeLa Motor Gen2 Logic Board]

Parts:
C61, C64: 22uF; C_1206_3216Metric
C62, C63, C65: 104; C_0402_1005Metric
D5: ESDCAN02; SOT-323_SC-70
D6: TVS 3.3V; D_SOD-123F
F1: Polyfuse; R_0603_1608Metric
R32, R33: 10*; R_0603_1608Metric
R34: 75k; R_0402_1005Metric
R35: 3.9k; R_0402_1005Metric
U14: ISOW7842F; SOIC-16W_7.5x10.3mm_P1.27mm
U15: MAX14775E; SOIC-8_3.9x4.9mm_P1.27mm

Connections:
+3V3: C61.1, C62.1, U14.1 (VCC); also elsewhere on the board
/RS485/3.3Viso: C63.1, C64.1, C65.1, R34.1, U14.16 (VISO), U15.8 (VCC)
/RS485/A: D5.1 (A1), R33.1; also elsewhere on the board
/RS485/B: D5.2 (A2), R32.1; also elsewhere on the board
/RS485/EXT_DI: U14.6 (OUTD); also elsewhere on the board
/RS485/ISO_DI: F1.1; also elsewhere on the board
/stm32/485_RX: U14.5 (OUTC); also elsewhere on the board
/stm32/485_TX: U14.4 (INB); also elsewhere on the board
/stm32/485_TXEN: U14.3 (INA); also elsewhere on the board
GND: C61.2, C62.2, U14.2 (GND1), U14.8 (GND1); also elsewhere on the board
GNDREF: C63.2, C64.2, C65.2, D5.3 (common), D6.2 (A), U14.9 (GND2), U14.10 (SEL), U14.15 (GND2), U15.5 (GND); also elsewhere on the board
unnamed: D6.1 (K), F1.2, R34.2, R35.1
unnamed: R32.2, U15.7 (B)
unnamed: R33.2, U15.6 (A)
unnamed: R35.2, U14.11 (IND)
unnamed: U14.12 (INC), U15.1 (RO)
unnamed: U14.13 (OUTB), U15.4 (DI)
unnamed: U14.14 (OUTA), U15.2 (~RE), U15.3 (DE)

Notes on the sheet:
0ZCM0002FF2G
SMF3.3

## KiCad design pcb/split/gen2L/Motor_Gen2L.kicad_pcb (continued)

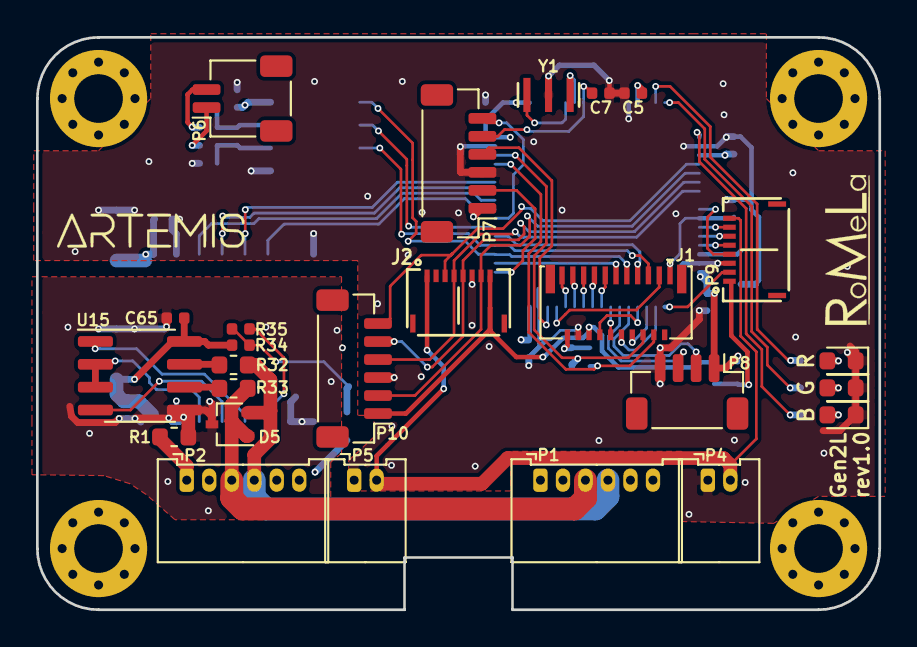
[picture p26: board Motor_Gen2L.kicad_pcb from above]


Board: 4 copper layers, 46.8 x 31.8 mm, 60 parts (29 on the bottom side), 71 nets.

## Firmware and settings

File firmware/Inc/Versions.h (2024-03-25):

/**
 * @file 	Versions.h
 * @brief 	Define firmware version for different motors
 *
 * @author 	Tym Zhu
 */
#ifndef VERSIONS_H
#define VERSIONS_H

/**
 * @name Motor defines uncomment the correct one
 * @{
 */
//#define MOTOR_KB01_R18  	/**< 0x01 KB01 (4006 with Ext AS5047) */
//#define MOTOR_KB01_R24  	/**< 0x02 KB01 (4006 with Ext AS5047) */
//#define MOTOR_U54			/**< 0x03 KB02 (U54) */
//#define MOTOR_U5412_R19  	/**< 0x04 KBMB00 (U5412 R19) */
//#define MOTOR_U5412_R20  	/**< 0x05 KBMB00 (U5412 R20) */
//#define MOTOR_U8			/**< 0x09 U8 (rev2) */
//#define MOTOR_U98			/**< 0x0A PB02&PB02P (U98) */
#define MOTOR_U180_HMND 	/**< 0x20 U180 ARTEMIS */
//#define MOTOR_U10P_HMND 	/**< 0x21 U10Plus ARTEMIS */
//#define MOTOR_4006_HMND 	/**< 0x22 4006 ARTEMIS */
//#define MOTOR_U5412_HMND	/**< 0x23 U5412/KBMB00 ARTEMIS */
//#define MOTOR_U5412_R20_HMND	/**< 0x24 U5412/KBMB00 R20 ARTEMIS */
//#define MOTOR_U54_HMND  	/**< 0x03 U54/KB02 ARTEMIS */
/**
 * @}
 */
/**
 * @name Motor defines for different variants
 * @{
 */
#ifdef MOTOR_U8		/*** U8 (rev2) ***/
	#define DRV_VERSION			3U		/**< Driver board version Gen2.0 */
	#define HW_VERSION			0x09	/**< motor hardware model */
	#define POLE_PAIR			21			//21 for U8
	#define REDUCTION_RATIO		10

	#define MOTOR_KM			0.98f//0.898f	// V/(rad/s) 
	#define MOTOR_R				0.173f		// Ohm

	#define DEFAULT_KP			0.456f
	#define DEFAULT_KI			0.027f

	/* Main Encoder */
	#define MHM_PV_MULTITURN	
	#define RTR_ENC_RES			65536
	#define RTR_ENC_RES_BIT		(16U)
	/* Ext Encoder */
	#define EXT_ENC_RES			1//No Ext Encoder

	#define AFC_HARMONIC2		12.0f

#endif

#ifdef MOTOR_U54	/*** U54 test (KB02) ***/
	#define DRV_VERSION			3U		/**< Driver board version Gen2.0 */
	#define HW_VERSION			0x03	/**< motor hardware model */
	#define POLE_PAIR			20
	#define REDUCTION_RATIO		9

	#define DEFAULT_KP			0.277f
	#define DEFAULT_KI			0.061f

	/* Main Encoder */
	#define MHM_NO_EEPROM
	static const uint8_t MHM_Regs[]=
						  {	0x11, 0x07, 0x00, 0x28, 0x80, 0x00, 0x00, 0x00, 0xC0, 0x80, 
							0x00, 0x00, 0x49, 0x00, 0x00, 0x00, 0x00, 0x00, 0x00, 0x8C};
	#define RTR_ENC_RES			65536
	#define RTR_ENC_RES_BIT		(16U)
	/* Ext Encoder */
	#define EXT_MA_ENCODER
	#define EXT_MA_BCT			190
	#define EXT_ENC_RES			65536

	#define AFC_HARMONIC2		2.0f

#endif

#if defined (MOTOR_U5412_R19) || defined (MOTOR_U5412_R20) 	/*** U5412 R19&20 (KBMB00) ***/
	#define DRV_VERSION			3U			/**< Driver board version Gen2.0 */
	#ifdef  MOTOR_U5412_R19
		#define HW_VERSION			0x04	/**< motor hardware model */
		#define REDUCTION_RATIO		19.191666666666667f
	#else //MOTOR_U5412_R20
		#define HW_VERSION			0x05	/**< motor hardware model */
		#define REDUCTION_RATIO		20
	#endif

	#define POLE_PAIR			20

	#define DEFAULT_KP			0.358f
	#define DEFAULT_KI			0.077f

	/* Main Encoder */
	#define MHM_NO_EEPROM
	static const uint8_t MHM_Regs[]=
						  {	0x11, 0x07, 0x00, 0x28, 0x80, 0x00, 0x00, 0x00, 0xC0, 0x80, 
							0x00, 0x00, 0x49, 0x00, 0x00, 0x00, 0x00, 0x00, 0x00, 0x8C};
	#define RTR_ENC_RES			65536
	#define RTR_ENC_RES_BIT		(16U)
	/* Ext Encoder */
	#define INIT_USE_EXT_ENC	//use external encoder value for init
	
	#define EXT_MA_ENCODER
	#define EXT_MA_BCT			183
	#define EXT_ENC_RES			65536

	#define AFC_HARMONIC2		2.0f

#endif
	
#ifdef MOTOR_U98	/*** U98 test (PB02) ***/
	#define DRV_VERSION			3U		/**< Driver board version Gen2.0 */
	#define HW_VERSION			0x0A	/**< motor hardware model */
	#define POLE_PAIR			40
	#define REDUCTION_RATIO		6

	#define DEFAULT_KP			0.099f
	#define DEFAULT_KI			0.039f

	/* Main Encoder */
//	#define MHM_NO_EEPROM
//	static const uint8_t MHM_Regs[]=
//						  {	0x11, 0x07, 0x00, 0x28, 0x80, 0x00, 0x00, 0x00, 0xC0, 0x80, 
//							0x00, 0x00, 0x49, 0x00, 0x00, 0x00, 0x00, 0x00, 0x00, 0x8C};
	#define MHM_PV_MULTITURN	
	#define RTR_ENC_RES			65536
	#define RTR_ENC_RES_BIT		(16U)
	/* Ext Encoder */
	#define NO_ABS_ENCODER
	#define EXT_ENC_RES			1//No Ext Encoder

	#define AFC_HARMONIC2		2.0f

#endif

#if defined (MOTOR_KB01_R18) ||	defined (MOTOR_KB01_R24) /*** 4006 with Ext AS5047 (KB01) ***/
	#define DRV_VERSION			3U			/**< Driver board version Gen2.0 */
	#ifdef  MOTOR_KB01_R18
		#define HW_VERSION			0x01	/**< motor hardware model */
		#define REDUCTION_RATIO		18
	#else //MOTOR_KB01_R24
		#define HW_VERSION			0x02	/**< motor hardware model */
		#define REDUCTION_RATIO		24
	#endif
	
	#define DEFAULT_KP			0.374f
	#define DEFAULT_KI			0.030f

	#define POLE_PAIR			12
	/* Main Encoder */
	#define MHM_NO_EEPROM
	static const uint8_t MHM_Regs[]=
						  {	0x10, 0x47, 0x00, 0x28, 0x80, 0x00, 0x00, 0x00, 0xC0, 0x80, 
						  	0x00, 0x00, 0xE1, 0x00, 0x00, 0x00, 0x00, 0x00, 0x00, 0x8C};
	#define RTR_ENC_RES			65536
	#define RTR_ENC_RES_BIT		(16U)
	/* Ext Encoder */
	#define EXT_AS_ENCODER
	#define EXT_ENC_RES			16384

	#define AFC_HARMONIC2		6.0f

#endif

#ifdef MOTOR_U180_HMND	/*** U180_HMND ARTEMIS ***/
	#define DRV_VERSION			4U		/**< Gen2 high current for ARTEMIS */
	#define HW_VERSION			0x20	/**< motor hardware model */
	#define POLE_PAIR			40
	#define REDUCTION_RATIO		5.93103448275862f
	
	#define DEFAULT_KP			0.293f
	#define DEFAULT_KI			0.017f

	/* Main Encoder */
	#define MU_PVL_MULTITURN
	#define RTR_ENC_RES			524288
	#define RTR_ENC_RES_BIT		(19U)
	/* Ext Encoder */
	#define EXT_ENC_RES			1//No Ext Encoder

	#define AFC_HARMONIC2		6.0f

#endif

#ifdef MOTOR_U10P_HMND	/*** U10Plus ARTEMIS ***/
	#define DRV_VERSION			3U		/**< Driver board version Gen2.0 */
	#define HW_VERSION			0x21	/**< motor hardware model */
	#define POLE_PAIR			20
	#define REDUCTION_RATIO		14.46153846153846f

	#define DEFAULT_KP			0.353f
	#define DEFAULT_KI			0.016f

	/* Main Encoder */
	#define MHM_PV_MULTITURN	
	#define RTR_ENC_RES			65536
	#define RTR_ENC_RES_BIT		(16U)
	/* Ext Encoder */
	#define EXT_ENC_RES			1//No Ext Encoder

	#define AFC_HARMONIC2		2.0f

#endif

#ifdef MOTOR_4006_HMND	/*** 4006 ARTEMIS ***/
	#define DRV_VERSION			3U		/**< Driver board version Gen2.0 */
	#define HW_VERSION			0x22	/**< motor hardware model */
	#define POLE_PAIR			12
	#define REDUCTION_RATIO		50.28099173553719f

	#define DEFAULT_KP			0.374f
	#define DEFAULT_KI			0.030f

	/* Main Encoder */
	#define MHM_PV_MULTITURN	
	#define RTR_ENC_RES			65536
	#define RTR_ENC_RES_BIT		(16U)
	/* Ext Encoder */
	#define EXT_ENC_RES			1//No Ext Encoder

	#define AFC_HARMONIC2		6.0f

#endif

#ifdef MOTOR_U5412_HMND	/*** U5412/KBMB00 ARTEMIS ***/
	#define DRV_VERSION			3U		/**< Driver board version Gen2.0 */
	#define HW_VERSION			0x23	/**< motor hardware model */
	#define POLE_PAIR			20
	#define REDUCTION_RATIO		19.19166666666667f

	#define DEFAULT_KP			0.358f
	#define DEFAULT_KI			0.077f

	/* Main Encoder */
	#define MHM_PV_MULTITURN	
	#define RTR_ENC_RES			65536
	#define RTR_ENC_RES_BIT		(16U)
	/* Ext Encoder */
	#define EXT_ENC_RES			1//No Ext Encoder

	#define AFC_HARMONIC2		2.0f

#endif
#ifdef MOTOR_U5412_R20_HMND	/*** U5412/KBMB00 R20 ARTEMIS ***/
	#define DRV_VERSION			3U		/**< Driver board version Gen2.0 */
	#define HW_VERSION			0x24	/**< motor hardware model */
	#define POLE_PAIR			20
	#define REDUCTION_RATIO		20.0f

	#define DEFAULT_KP			0.358f
	#define DEFAULT_KI			0.077f

	/* Main Encoder */
	#define MHM_PV_MULTITURN
	#define RTR_ENC_RES			65536
	#define RTR_ENC_RES_BIT		(16U)
	/* Ext Encoder */
	#define EXT_ENC_RES			1//No Ext Encoder

	#define AFC_HARMONIC2		2.0f

#endif
	
#ifdef MOTOR_U54_HMND	/*** U54/KB02 ARTEMIS ***/
	#define DRV_VERSION			3U		/**< Driver board version Gen2.0 */
	#define HW_VERSION			0x03	/**< motor hardware model */
	#define POLE_PAIR			20
	#define REDUCTION_RATIO		9

	#define DEFAULT_KP			0.277f
	#define DEFAULT_KI			0.061f

	/* Main Encoder */
	#define MHM_PV_MULTITURN	
	#define RTR_ENC_RES			65536
	#define RTR_ENC_RES_BIT		(16U)
	/* Ext Encoder */
	#define EXT_ENC_RES			1//No Ext Encoder

	#define AFC_HARMONIC2		2.0f

#endif
/**
 * @}
 */
#endif

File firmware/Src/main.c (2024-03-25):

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
/* Includes ------------------------------------------------------------------*/
#include "main.h"


/* USER CODE BEGIN Includes */
#include "Config.h"

#include "IC_MHM_PV.h"
#include "IC_MU_PVL.h"
#include "DRV8320.h"
#include "TMP112.h"
//#include "MAX31855.h"
#include "ADS8353.h"
//#include "AS5311.h"
#include "MPS_MA.h"
#include "Flash.h"

#include "util.h"
//#include "Control_LL.h"
#include "Control.h"
//#include "Data_Comm.h"
//#include "Error.h"
//#include "Multiturn_Enc.h"
	  
/* USER CODE END Includes */

ADC_HandleTypeDef hadc1;

CRC_HandleTypeDef hcrc;

I2C_HandleTypeDef hi2c1;

SPI_HandleTypeDef hspi1;
SPI_HandleTypeDef hspi2;
SPI_HandleTypeDef hspi3;
DMA_HandleTypeDef hdma_spi1_rx;
DMA_HandleTypeDef hdma_spi1_tx;
DMA_HandleTypeDef hdma_spi2_tx;
DMA_HandleTypeDef hdma_spi2_rx;

TIM_HandleTypeDef htim1;
TIM_HandleTypeDef htim5;
TIM_HandleTypeDef htim6;
TIM_HandleTypeDef htim7;

UART_HandleTypeDef huart1;
USART_HandleTypeDef husart3;
UART_HandleTypeDef huart6;
DMA_HandleTypeDef hdma_usart1_tx;
DMA_HandleTypeDef hdma_usart6_tx;

/* USER CODE BEGIN PV */

Motor_TypeDef Motor1;	/**< motor controller structure */
//Debug_TypeDef Debug;	//not in use
Mode_TypeDef  Mode;		/**< actuator mode structure */

Motor_Config_TypeDef  Config_Active;	/**< active config */
Motor_Config_TypeDef  Config_Buff;		/**< buffered config */
/** config data from flash */
Motor_Config_TypeDef* pConfig_Flash = (Motor_Config_TypeDef*)CONFIG_ADD;

Motor_Stat_TypeDef Stat_Active;			/**< active stats */
Motor_Stat_TypeDef Stat_Buff;			/**< buffered stats */

/** calibration data from flash */
Cal_TypeDef* pCal_Flash = (Cal_TypeDef*)CAL_ADDR;


volatile uint32_t idle_ct=0;		/**< counter for cpu idle counter */
volatile uint8_t idle_refresh=0;	/**< reset for cpu idle counter */

	
/* USER CODE END PV */

void SystemClock_Config(void);
static void MX_GPIO_Init(void);
static void MX_DMA_Init(void);
static void MX_SPI1_Init(void);
static void MX_SPI2_Init(void);
static void MX_SPI3_Init(void);
static void MX_TIM1_Init(void);
static void MX_ADC1_Init(void);
static void MX_I2C1_Init(void);
static void MX_USART1_UART_Init(void);
static void MX_USART6_UART_Init(void);
static void MX_TIM5_Init(void);
static void MX_TIM6_Init(void);
static void MX_TIM7_Init(void);
static void MX_CRC_Init(void);
static void MX_USART3_Init(void);
/* USER CODE BEGIN PFP */

/* USER CODE END PFP */

/**
  * @brief  The application entry point.
  * @retval int
  */
int main(void)
{
  /* USER CODE BEGIN 1 */
	uint8_t MHM_ReadBack[20];
	
	/*** check for data size ***/
	static_assert(sizeof(Motor_Stat_TypeDef)==4*MOTOR_STAT_SIZE,
				  "stat data size should be MOTOR_STAT_SIZE");	
	static_assert(sizeof(Motor_Config_TypeDef)==4*MOTOR_CONFIG_SIZE,
				  "Flash data size should be MOTOR_CONFIG_SIZE");
	static_assert(sizeof(Cal_TypeDef)==4*CAL_SIZE,
				  "Flash data size should be CAL_SIZE");
	
  /* USER CODE END 1 */

  /* MCU Configuration--------------------------------------------------------*/

  /* Reset of all peripherals, Initializes the Flash interface and the Systick. */
  HAL_Init();

  /* Configure the system clock */
  SystemClock_Config();

  /* Initialize all configured peripherals */
  MX_GPIO_Init();
  MX_DMA_Init();
  MX_SPI1_Init();
  MX_SPI2_Init();
  MX_SPI3_Init();
  MX_TIM1_Init();
  MX_ADC1_Init();
  MX_I2C1_Init();
  MX_USART1_UART_Init();
  MX_USART6_UART_Init();
  MX_TIM5_Init();
  MX_TIM6_Init();
  MX_TIM7_Init();
  MX_CRC_Init();
  MX_USART3_Init();
  /* USER CODE BEGIN 2 */
	
	/*** Start initialization ***/
	/* Print out hardware driver and firmware version number */
	printf("Version HW:%02X DRV:%02X FW:%04X\n", HW_VERSION, DRV_VERSION, FW_VERSION);
	
	/*** Initialize indicator LEDs PWM ***/
	HAL_TIM_PWM_Start(&htim5,TIM_CHANNEL_2);
	HAL_TIM_PWM_Start(&htim5,TIM_CHANNEL_3);
	HAL_TIM_PWM_Start(&htim5,TIM_CHANNEL_4);
	
	/* Light up red led when initializing*/
	LED_R_dim(); LED_G_off(); LED_B_off();
	
	
	/*** DRV8320 reset ***/
	__HAL_SPI_ENABLE(&HSPI_DRV8320);
	DRV8320_Reset();	// DRV8320 reset pin pulse
	
	/*** Main Encoder ***/
#ifdef MHM_NO_EEPROM
	/* MHM w/o EEPROM and PV */
	HAL_Delay(45);		// Delay waiting for EEPROM read timeout
//	MHM_Read_Regs(0x00, 20);
	
	/* Overwrite MHM Registers */
	printf("MHM Writing EEPROM..");
	do {
		printf(".");
		MHM_Write_Regs(0x00, (uint8_t*)MHM_Regs, 20);	// Write all registers
		DelayMicros(1);
		MHM_Write_Reg(MHM_ADDR_RESET, MHM_INSTR_RESET);	// Reset MHM
		HAL_Delay(14);
		MHM_Read_Regs(0x00, 20, MHM_ReadBack);
		
	} while( memcmp(MHM_Regs, MHM_ReadBack, 20) );	//readback check
	
	printf("  DONE\n");	//MHM registers set success!
	/* Print MHM registers and errors for debug */
	printf("MHM Reg:%02X %02X %02X %02X Err:%02X\n", MHM_ReadBack[0],
													 MHM_ReadBack[1],
													 MHM_ReadBack[2],
													 MHM_ReadBack[3],
											MHM_Read_Reg(MHM_ADDR_ERROR));
	/* Print MHM Gain */
	printf("MHM Gain: %04X\n", MHM_Read_Reg(MHM_ADDR_GAINS));
	
#elif defined(MHM_PV_MULTITURN)
	/* MHM w/ PV Multiturn */
	/* Registers auto loaded from EEPROM */
	HAL_Delay(20);	//Enough delay to have ic-MU power on.
	
//	/* DEBUG */
//	USART_PutChar(USART_DEBUG,MHM_Read_Reg(MHM_ADDR_GAINS));
//	USART_PutChar(USART_DEBUG, MHM_Read_Posi(&Motor1.Rtr_MT, &Motor1.Rtr_ST));
//	HAL_Delay(1);

	/* Print MHM Gain */
	printf("MHM Gain: %04X\n", MHM_Read_Reg(MHM_ADDR_GAINS));	
	
#elif defined(MU_PVL_MULTITURN)
	/* MU w/ PVL Multiturn */
	/* Registers auto loaded from EEPROM */
	HAL_Delay(20);	//Enough delay to have ic-MU power on. 
	
//	USART_PutChar(USART_DEBUG, MU_Read_Reg(MU_ADDR_ACGAIN_M));
//	HAL_Delay(1);
	/* Print MU status bits */
	printf("MU Stats 0 1: %02X %02X\n", MU_Read_Reg(MU_ADDR_STATUS0), 
		   								MU_Read_Reg(MU_ADDR_STATUS1) );
	/* Print MU Gain */
	printf("MU Gains M N: %02X %02X\n", MU_Read_Reg(MU_ADDR_ACGAIN_M), 
		   								MU_Read_Reg(MU_ADDR_ACGAIN_N) );	
	
#else
	#error "Main Encoder definition invalid!"
#endif

	
	/*** TMP112 initialize ***/
	printf("TMP Writing Configs... ");
	while ( TMP112_WriteConfig(TMP112_ADDR0, TMP112_8HZ, TMP112_EXTENDED_MODE) != HAL_OK );
	printf("DONE\n");
	//printf("\n%04d TMP112 init Done", Get_Tick_Diff());
	
	/*** DRV8320 Initialize ***/	
	printf("DRV Writing Configs... ");
	while ( DRV8320_Write_Confirm(DRV_ADDR_GDHS,
									(0x03<<DRV_GDHS_LOCK_Pos)|			//0x03 unlock
				  					(IDRIVE_CURRENT<<DRV_GDHS_IDRIVEP_HS_Pos)|	//0x01 30mA
									(IDRIVE_CURRENT<<DRV_GDHS_IDRIVEN_HS_Pos))	//0x01 60mA
		   						  != HAL_OK );	
	while ( DRV8320_Write_Confirm(DRV_ADDR_GDLS,
									(0x01<<DRV_GDLS_CBC_Pos)|			//0x01
				  					(0x02<<DRV_GDLS_TDRIVE_Pos)|		//0x02 2000-ns peak drive time
				  					(IDRIVE_CURRENT<<DRV_GDLS_IDRIVEP_LS_Pos)|	//0x01 30mA
									(IDRIVE_CURRENT<<DRV_GDLS_IDRIVEN_LS_Pos)) 	//0x01 60mA
								  != HAL_OK );	
	while ( DRV8320_Write_Confirm(DRV_ADDR_OCP, 
								  	(0x00<<DRV_OCP_DEADTIME_Pos)|		//0x00 50ns
				  					(0x00<<DRV_OCP_MODE_Pos)|			//0x00 latch fault
				  					(0x02<<DRV_OCP_DEG_Pos)|			//0x02 6us
									(VDS_OVERCURRENT<<DRV_OCP_VDS_LVL_Pos))		//0x04 0.31V
		  						  != HAL_OK );	
	while ( DRV8320_Write_Confirm(DRV_ADDR_DCTRL,
								  	(0x01<<DRV_DC_PWM_MODE_Pos)|		//0x01 3PWM mode
								 	(0x00<<DRV_DC_CLR_FLT_Pos))			//0x00 do not clear fault
		   						  != HAL_OK );	
	printf("DONE\n");
	/* Print DRV8320 register values */
	printf("DRV Registers: %03x %03x %03x %03x %03x %03x\n", 
		   	DRV8320_Read(DRV_ADDR_FAULT1),DRV8320_Read(DRV_ADDR_FAULT2),DRV8320_Read(DRV_ADDR_DCTRL),
			DRV8320_Read(DRV_ADDR_GDHS),DRV8320_Read(DRV_ADDR_GDLS),DRV8320_Read(DRV_ADDR_OCP) );

	/*** ADS8353 Initialize ***/
	printf("ADS Writing Configs... ");
	ADS8353_DMA_Init();
	while( ADS8353_Write_Confirm_Reg(ADS_WRITE_CFR, ADS_READ_CFR,
									 (0<<ADS_RD_CLK_MODE_Pos)|		//32-CLK mode
					  				 (1<<ADS_RD_DATA_LINES_Pos)|	//use only SDO_A
									 (1<<ADS_INPUT_RANGE_Pos)|		//2xVref FSR
									 (0<<ADS_INM_SEL_Pos)|			//single-ended
									 (1<<ADS_REF_SEL_Pos)|			//internal reference
									 (0<<ADS_STANDBY_Pos)|			//not in standby
									 (0<<ADS_RD_DATA_FORMAT_Pos))	//straight binary
									!= HAL_OK );
	printf("DONE\n");
	printf("ADS CFR: %03X REFDAC: %03X %03X \n", ADS8353_Read_Reg(ADS_READ_CFR)&0xFFF,
												(ADS8353_Read_Reg(ADS_READ_REFDAC_A)&0xFFF)>>3,
												(ADS8353_Read_Reg(ADS_READ_REFDAC_B)&0xFFF)>>3);

	/*** External Encoders ***/

#ifdef EXT_MA_ENCODER
	/* MA310 external encoder for output shaft absolute position */
	printf("EXT MA Writing Configs...");
	
	while( MA_Write_Confirm_Reg(MA_ADDR_ET, 0x02)	// Y direction
								!= HAL_OK );
	while( MA_Write_Confirm_Reg(MA_ADDR_BCT, EXT_MA_BCT)	// BCT value
								!= HAL_OK );
	while( MA_Write_Confirm_Reg(MA_ADDR_RD, 0x80)	// CCW
								!= HAL_OK );
	printf("0x02/3/9: %02X %02X %02X\n", MA_Read_Reg(0x02),
										 MA_Read_Reg(0x03),
										 MA_Read_Reg(0x09) );
#endif
	
	/*** Controller initialize sequence ***/
	Ctrl_Init();
	
    /*** PWM Initialize ***/
    /* Set Interupt */
	__HAL_TIM_DISABLE_IT(&htim1, (TIM_IT_UPDATE | TIM_IT_CC1 | TIM_IT_CC2 | TIM_IT_CC3 |
								  TIM_IT_COM | TIM_IT_TRIGGER | TIM_IT_BREAK));
	__HAL_TIM_ENABLE_IT(&htim1, TIM_IT_CC4);
    /* Set the Capture Compare Register value */
    TIM1->CCR1 = HALF_PWM_CCR; //V1_A
    TIM1->CCR2 = HALF_PWM_CCR; //V1_B
    TIM1->CCR3 = HALF_PWM_CCR; //V1_C
    TIM1->CCR4 = 0x001; //ADC
    /* Enable output */
    TIM_CCxChannelCmd(htim1.Instance, TIM_CHANNEL_1, TIM_CCx_ENABLE);
    TIM_CCxChannelCmd(htim1.Instance, TIM_CHANNEL_2, TIM_CCx_ENABLE);
    TIM_CCxChannelCmd(htim1.Instance, TIM_CHANNEL_3, TIM_CCx_ENABLE);
    TIM_CCxChannelCmd(htim1.Instance, TIM_CHANNEL_4, TIM_CCx_ENABLE);
    __HAL_TIM_MOE_ENABLE(&htim1);
	__HAL_TIM_ENABLE(&htim1); //Start TIM1

	/*** Enable control loops ***/
    HAL_TIM_Base_Start_IT(&htim7);      //4000Hz Controls
    HAL_TIM_Base_Start_IT(&htim6);      //5Hz
	
	/***********finish initialize*********/
	LED_R_off();	
	LED_G_dim();	//Green LED 
	

	
  /* USER CODE END 2 */

  /* Infinite loop */
  /* USER CODE BEGIN WHILE */
	while (1)
	{
    /* USER CODE END WHILE */

    /* USER CODE BEGIN 3 */
		
	/*** Count idle for CPU percentage monitoring ***/
		idle_ct++;
		if (idle_refresh)
		{
			idle_ct = 0;
			idle_refresh = 0;
		}
		
	}
  /* USER CODE END 3 */
}

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
/* USER CODE BEGIN 4 */







/* re-direct printf to SWO */
int __io_putchar(int ch)
{
	// Write character to ITM ch.0
	ITM_SendChar(ch);
	return (ch);
}





/* USER CODE END 4 */
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


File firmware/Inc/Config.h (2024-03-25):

/**
 * @file 	Config.h
 * @brief 	Configuration file for motor
 *
 * @author 	Tym Zhu
 */
/* Define to prevent recursive inclusion -------------------------------------*/
#ifndef CONFIG_H
#define CONFIG_H

/* macro for quick math */
#ifndef max
#define max(a,b) ((a) > (b) ? (a) : (b))
#endif
#ifndef min
#define min(a,b) ((a) < (b) ? (a) : (b))
#endif
//to limit the max absolute amount
#ifndef coerce
#define coerce(data,limit) ((data) > 0 ? (min(data,limit)) : (max(data,-limit)))
#endif
#ifndef abs
#define abs(x) ((x)<0 ? (-(x)) : (x))
#endif
#ifndef deadband
#define deadband(data,limit) ((abs(data)) > limit ? ( (data) > 0 ? (data-limit):(data+limit) ) : (0))
#endif

/* Includes ------------------------------------------------------------------*/

//#include "main.h"


#include "PID_f32.h"
#include "Build.h"
#include "Versions.h"


/* Private define ------------------------------------------------------------*/

/**** Defines for driver PCB configuration ***/


#if (DRV_VERSION == 3U)

	/* I_A_RAW = (ADC_Value-Neutral) * ADC_GAININV */
	#define ADC_GAININV			3.814697266E-3f	/**< 5.0V/(0.001Ohm*20*65536)
	 	 	 	 	 	 	 	 	 	 	 	 	 2.5V/20/0.001Ohm = +-125A */

	#define DOUBLE_PWM_FREQ						/**< double pwm frequency to 44kHz */

	#define IDRIVE_CURRENT		0x01			/**< 0x01 30mA/60mA */
	#define VDS_OVERCURRENT		0x04			/**< 0x04 0.31V
	 	 	 	 	 	 	 	 	 	 	 	 	 2.1mOhm*1.8*100A = 0.38V */

	#define CONFIG_IQ_MAX		100.0f			/**< Iq max allowed */
	#define CONFIG_TEMPERATURE_MAX 125.0f			/**< Temperature max allowed */


#elif (DRV_VERSION == 4U)

	/* I_A_RAW = (ADC_Value-Neutral) * ADC_GAININV */
	#define ADC_GAININV			0.00762939453125f /**< 5.0V/(0.0005Ohm*20*65536)
	 	 	 	 	 	 	 	 	 	 	 	 	   2.5V/20/0.5mOhm = +-250A */

	#define IDRIVE_CURRENT		0x02			/**< 0x01 60mA/120mA */
	#define VDS_OVERCURRENT		0x04			/**< 0x04 0.31V
	 	 	 	 	 	 	 	 	 	 	 	 	 0.91mOhm*1.8*200A = 0.33V */
	#define CONFIG_IQ_MAX		200.0f			/**< Iq max allowed */
	#define CONFIG_TEMPERATURE_MAX 2048.0f			/**< Temperature max allowed */

#else
	#error "DRV_VERSION define error!"
#endif
/**
 * @name PWM output
 * @{
 */
/** max pwm ratio for 3 phase pwm */
#define MAX_PWM_RATIO   	1.0f//0.94f//0.949f

#ifdef DOUBLE_PWM_FREQ
	/* PWM frequency doubled to 44kHz, controller still runs at 22kHz */
	#define PWM_CCR				2048	/**< 180MHz / (2048 + 1) /2 = 43924Hz */

#else

	#define PWM_CCR				4096	/**< 180MHz / (4096 + 1) /2 = 21973Hz */

#endif
//#define PWM_CCR				2048//4096
#define MAX_PWM_CCR_F		((float32_t)PWM_CCR)			/**< float32 PWM CCR */
#define HALF_PWM_CCR		(PWM_CCR/2)						/**< 1/2 PWM CCR */
#define SQRT3_PWM_CCR_F		(1.73205080757f*MAX_PWM_CCR_F)	/**< sqrt(3) PWM CCR */

/* max Vd Vq allowed (1.0) */
#define MAX_Vd 				0.5f		/**< maximum Vd */
#define MAX_Vq 				1.0f		/**< maximum Vq */
/**
 * @}
 */

/**
 * @name ADC
 * @{
 */

#define ADC_MID				0x8000		/**< ADC mid point */

/**
 * @}
 */

/**
 * @name Encoders
 * @{
 */
/* Encoder resolution */
//Moved to Versions.h
/** Convert Encoder count to degree */
#define K_THETA_E			((float32_t)(360.0f*POLE_PAIR/RTR_ENC_RES))	//POLE_PAIR*360/RTR_ENC_RES

/*** Multi-turn ***/

/** max number of turns at output shaft */
#define MAX_TURN			16
/** full resolution of rotor with max number of turns */
#define RTR_THETA_FULL_RES	((int64_t)(MAX_TURN*REDUCTION_RATIO*RTR_ENC_RES))
/** minimum rotor theta with number of turns */
#define RTR_THETA_MIN		((int64_t)(-MAX_TURN*REDUCTION_RATIO*RTR_ENC_RES/2))
/** float32 full resolution of rotor with max number of turns */
#define THETA_FULL_RES_F	((float32_t)(MAX_TURN*2.0f*PI))
/** float32 minimum rotor theta with number of turns */
#define THETA_MIN_F			((float32_t)(-MAX_TURN*PI))	//Theta >= THETA_MIN_F
/** float32 maximum rotor theta with number of turns */
#define THETA_MAX_F			((float32_t)(MAX_TURN*PI))	//Theta < THETA_MAX_F


/*** External Absolute Encoder ***/
//#define EXT_ABS_ENC

/**
 * @}
 */
/**
 * @name Loops
 * @{
 */
/* Calculate the ratio between two loop */
#define HIGH_LOOP_HZ		21973					/**< high freq loop frequency */
#define HIGH_LOOP_US		(1000000/HIGH_LOOP_HZ)	/**< high freq loop time in micro seconds */
#define MID_LOOP_HZ			4000					/**< mid freq loop frequency */
#define MID_LOOP_TIME		(1.0f/MID_LOOP_HZ)		/**< mid freq loop time in seconds */

/* Velocity constant */

/** convert theta dot to rad/s */
#define RtrThetaDot2RAD	(2.0f*PI/RTR_ENC_RES*HIGH_LOOP_HZ/REDUCTION_RATIO)	//diff/RTR_RES*2pi*HIGH_LOOP_HZ
/** convert theta to rad */
#define RtrTheta2RAD	(2.0f*PI/RTR_ENC_RES/REDUCTION_RATIO)
/** convert rad to theta in encoder res */
#define RAD2RtrTheta	(1.0f/RtrTheta2RAD)

/** convert external theta dot to rad/s */
#define ExtThetaDot2RAD	(2.0f*PI/EXT_ENC_RES*MID_LOOP_HZ)	//
/** convert external theta to rad */
#define ExtTheta2RAD	(2.0f*PI/EXT_ENC_RES)

/**
 * @}
 */

/**
 * @name Vbus sensing
 * @{
 */
#define K_Vbus_ADC		1.629920373E-2f	/**< Vbus conversion 3.3/2^12/(3.9/(3.9+75)) */
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

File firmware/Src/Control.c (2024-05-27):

/**
 * @file 	Control.c
 * @brief 	Controllers
 *
 * @author 	Tym Zhu
 */
#include "Control.h"

#include "IC_MHM_PV.h"
#include "IC_MU_PVL.h"
#include "DRV8320.h"
#include "TMP112.h"
#include "MAX31855.h"
#include "ADS8353.h"
#include "AS5311.h"
#include "MPS_MA.h"
#include "Flash.h"

#include "util.h"

#include "Control_LL.h"
#include "Data_Comm.h"
#include "Error.h"
#include "Multiturn_Enc.h"

volatile uint8_t MidCR_Refresh = 0;		/**< reset for mid speed control loop counter */
volatile uint32_t MidCR_Count = 0;		/**< counter for mid speed control loop */
volatile uint8_t ADCR_Refresh = 0;		/**< reset for high speed control loop counter */
volatile uint32_t ADCR_Count = 0;		/**< counter for high speed control loop */

uint16_t DRV8305_REG[6];				/**< DRV8305 register buffer */

/* UART6 debug port */
uint8_t Debug_Buff[65];					/**< buffer for Sending data to debug port */

/** turn debug buffer uint8_t* into float32_t*
  * First byte of debug buffer reserved for 0xff.
  */
volatile float32_t (*Debug_Data_f)[16] = (float32_t (*)[16]) (Debug_Buff + 1);

arm_biquad_casd_df1_inst_f32 IIR_Vbus;		/**< IIR instance for Vbus */
float32_t IIR_Vbus_State[4];				/**< IIR states for Vbus */
arm_biquad_casd_df1_inst_f32 IIR_Posi_ref;	/**< IIR instance for reference position */
float32_t IIR_Posi_ref_State[4];			/**< IIR states for reference position */
//arm_biquad_casd_df1_inst_f32 IIR_TempTC;
//float32_t IIR_TempTC_State[4];

float32_t JointLimitP = 200;		//P gain for joint limit
float32_t JointLimitOffset = 0.1;	//offset for joint limit

/* private function */
void Debug_Terminal();
static inline void ADC_Debug();
static inline void Ctrl_Debug();

/**
 * @brief Initialize controller
 *
 */
void Ctrl_Init()
{
	uint32_t Calculated_CRC;
	uint32_t MHM_CT = 0;

	/*** Check Flash for Calibration data & Motor Config ***/

	/* Calculate CRC for calibration data in flash */
	printf("Motor Cal CRC from flash: 0X%08lX\n", *(uint32_t*) CAL_CRC_ADDR);
	Calculated_CRC = CRC_Calc((uint32_t*) pCal_Flash, CAL_SIZE);

	/* Check calculated CRC against flash */
	if (Calculated_CRC != *(uint32_t*) CAL_CRC_ADDR)
	{
		/* Failed CRC test */
		printf("Motor Cal CRC FAILED!   : 0X%08lX\n", Calculated_CRC);
		printf("Calibration needed! \n");
		/* ERROR: calibration data invalid */
		Error_Set(ERROR_INIT);
	}
	else
	{
		/* Passed the CRC test*/
		printf("Motor Cal CRC SUCCESS! :  0X%08lX\n", Calculated_CRC);
	}

	/* Calculate CRC for motor config in flash */
	Calculated_CRC = CRC_Calc((uint32_t*) pConfig_Flash, MOTOR_CONFIG_SIZE);
	printf("Motor config CRC from flash: 0X%08lX\n",
			*(uint32_t*) CONFIG_CRC_ADD);
	/* Check calculated CRC against flash */
	if (Calculated_CRC != *(uint32_t*) CONFIG_CRC_ADD)
	{
		/* Failed CRC test */
		printf("Motor config CRC FAILED!  : 0X%08lX\n\n", Calculated_CRC);
		printf("Reset motor config to default..\n");
		/*reset flash if failed CRC test*/
		if (Write_Motor_Config((Motor_Config_TypeDef*) &Config_Default) != 0)
			printf("Reset motor config to default failed!\n");
		else
			printf("Reset motor config to default success!\n");
	}
	else
	{
		/* Passed the CRC test*/
		printf("Motor config CRC SUCCESS! :  0X%08lX\n", Calculated_CRC);
	}

	/* Load Config from flash */
	Config_Buff = Config_Active = *pConfig_Flash;

	/*** Setup inital values for motor structure ***/
	Motor1.Rtr_Elec_Offset = pCal_Flash->Elec_Offset;
	Motor1.Rtr_Theta_Offset32 = (int32_t) ((pCal_Flash->Theta_Zero_Offset
			+ Config_Active.Homing_Offset + 0) * RAD2RtrTheta);
	Motor1.Rtr_MT_Offset = Config_Active.Rtr_MT_Offset;
	Motor1.ADC_A_Zero = ADC_MID + pCal_Flash->ADC_A_Offset;
	Motor1.ADC_B_Zero = ADC_MID + pCal_Flash->ADC_B_Offset;

	Motor1.Max_Iq = Config_Active.I_Max;
	Motor1.Max_ThetaDot = Config_Active.Velo_Max;
	Motor1.Max_ThetaDotDot = Config_Active.Acc_Max;

	/*** Encoder finding absolute position ***/
#ifdef MHM_PV_MULTITURN
	/* MHM w/ ic-pv Multiturn enabled */
	/* Try reading MT and ST from MHM */
	while ((MHM_Read_Posi(&Motor1.Rtr_MT, &Motor1.Rtr_ST) & (MHM_POS_NERR)) == 0x00)
	{
		/* try max MHM_BOOTUP_TIME */
		if (MHM_CT == MHM_BOOTUP_TIME) break;
		HAL_Delay(1);
		MHM_CT++;
	}
	if (MHM_CT == MHM_BOOTUP_TIME)
	{
		/* MHM still has error after MHM_BOOTUP_TIME */
		/* Check MHM error register */
		if ( MHM_Read_Reg(MHM_ADDR_ERROR) & 
			(MHM_ERR_CFG| MHM_ERR_OFFS| MHM_ERR_POS|
			 MHM_ERR_AMIN| MHM_ERR_AMAX| MHM_ERR_MTI) )
		{
			Error_Set(ERROR_INIT);
		}
	}
	
#elif defined(EXT_MA_ENCODER) || defined(EXT_AS_ENCODER)

#ifdef INIT_USE_EXT_ENC
	
		MHM_Read_Posi(&Motor1.Rtr_MT, &Motor1.Rtr_ST);	//get rotor postion
		/* get absolute encoder position */
		#ifdef EXT_MA_ENCODER
			Motor1.Ext_Theta_Raw_Prev = Motor1.Ext_Theta_Raw = MA_Read_Posi();
		#else	//EXT_AS_ENCODER
			Motor1.Ext_Theta_Raw_Prev = Motor1.Ext_Theta_Raw = AS5311_Simple_Read_Fast();
		#endif
		/* use ext theta directly */
		Motor1.Ext_Theta = ExtTheta2RAD * Motor1.Ext_Theta_Raw - PI;	
		printf("Ext_Theta:%.4f \n",  Motor1.Ext_Theta);
		/* Set MT offset = 0 */
		Motor1.Rtr_MT_Offset = Config_Active.Rtr_MT_Offset 
							 = Config_Buff.Rtr_MT_Offset = 0;
		/* Rtr Theta with MT offset = 0 */
		Motor1.Rtr_Theta_64 = (int64_t)(Motor1.Rtr_MT + Motor1.Rtr_MT_Offset) * RTR_ENC_RES 
						  	+ Motor1.Rtr_ST;
		Motor1.Rtr_Theta = WrapRtrTheta64(Motor1.Rtr_Theta_64 + Motor1.Rtr_Theta_Offset32) 
							* RtrTheta2RAD;
		printf("Rtr_Theta:%.4f \n",  Motor1.Rtr_Theta);
		/* find difference */
		printf("Rtr_Theta_Offset32:%ld \n",  Motor1.Rtr_Theta_Offset32);
		
		Motor1.Ext_Theta_ZeroOffset = Motor1.Ext_Theta - Motor1.Rtr_Theta;
		printf("Ext_Theta_ZeroOffset:%.4f \n",  Motor1.Ext_Theta_ZeroOffset);
		/* update offset */
		Motor1.Rtr_Theta_Offset32 = (int32_t)((pCal_Flash->Theta_Zero_Offset 
										   + Config_Active.Homing_Offset + Motor1.Ext_Theta_ZeroOffset)*RAD2RtrTheta);
		printf("Rtr_Theta_Offset32:%ld \n",  Motor1.Rtr_Theta_Offset32);
		/* double check rtr theta */
		Motor1.Rtr_Theta = WrapRtrTheta64(Motor1.Rtr_Theta_64 + Motor1.Rtr_Theta_Offset32) 
							* RtrTheta2RAD;
		printf("Rtr_Theta:%.4f \n",  Motor1.Rtr_Theta);
//		printf("Use Ext Theta:%.4f Theta Offset:%d Rtr Theta:%.4f \n",  Motor1.Ext_Theta,
//			   															Motor1.Rtr_Theta_Offset32,
//																		Motor1.Rtr_Theta );
		
	#else
	/* External MA or AS encoder */
	printf("Finding absolute position... ");

	do
	{
		if (MHM_CT == MHM_BOOTUP_TIME)
			break;
		MHM_Read_Posi(&Motor1.Rtr_MT, &Motor1.Rtr_ST);	//get rotor postion
		/* get absolute encoder position */
#ifdef EXT_MA_ENCODER
		Motor1.Ext_Theta_Raw_Prev = Motor1.Ext_Theta_Raw = MA_Read_Posi();
#else	//EXT_AS_ENCODER
				Motor1.Ext_Theta_Raw_Prev = Motor1.Ext_Theta_Raw = AS5311_Simple_Read_Fast();
			#endif

		MHM_CT++;

	} while (MLT_Init_MT(Motor1.Rtr_ST, Motor1.Rtr_MT, Motor1.Ext_Theta_Raw)
			!= 0);
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

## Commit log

2024-03-25 Initial commit based on archive from 12/6/2022
    [Current_ADC.sch, Driver_Gen2Rev1_BOM.xls, Encoder.sch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]
2024-05-27 Limit joint torque towards joint limits.
2025-09-29 updated schematics and added split PCB.
    [Current_ADC.sch, Driver_Gen2L_rev1_BOM.xls, Driver_Gen2P_rev1_BOM.xls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]

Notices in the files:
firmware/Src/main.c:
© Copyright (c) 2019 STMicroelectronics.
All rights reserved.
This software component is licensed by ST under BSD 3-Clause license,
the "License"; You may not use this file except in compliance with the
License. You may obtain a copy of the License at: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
